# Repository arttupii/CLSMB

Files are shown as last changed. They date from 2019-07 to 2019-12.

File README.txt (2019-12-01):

Closed loop step motor controller

Two modes are supported. Step loss compensation and load position control mode.
You can select mode from config.h file.
     
    Architecture of closed loop step motor controller:

                                             +---------+--------+
                        +---------------+    | Rotary  |  Step  |
                        |               |    | encoder |  Motor |
                        |               |    |         |        |
                        |               |    |         |        |
           stepIn------>|D8             |    |         |        |
                        |   Arduino     |    |         |        |
           dirIn------->|D9 Nano        |    |  A   B  |        |
                        |               |    +---------+--------+
           EnIn-------->|D10            |       |   |     ^^^^
                        |               |IN_A   |   |     ||||
           LED---------<|D13          D2|<------+   |     ||||
                        |               |           |     ||||
        _________       |               |IN_B       |     ||||
        FEED HOLD------<|D7           D3|<----------+     ||||
                        |               |                 ||||
                        |  A2  A1  A0   |                 ||||
                        +---------------+                 ||||
                           |   |   |                      ||||
                           |   |   |                      ||||
                           V   V   V                      ||||
                        +---------------+                 ||||
                        | !EN DIR  STEP |                 ||||
                        |               |                 ||||
                        |  Standard    A|-----red---------+|||
                        |              _|                  ||| 
                        |  Stepmotor   A|-----blue---------+||
                        |               |                   ||  
                        |  controller  B|-----green---------+|
                        |              _|                    |
                        |  e.g. TB6600 B|-----black----------+
                        |               |
                        |               |
                        +---------------+                   

Block diagram (STEP_LOSS_COMPENSATION-mode)
                   +----------------------------------+  
                   |   +----------+                   |  
 Input(Step,En,Dir)|   | Input    |                   |                                             
 ------------------+-->| counter  |                   |                                                  
                       |          |                   |              +--------------+       +--------------+
                   +---|          |                   |              |              |       | Step Motor   |
                   |   +----------+                   V    (Switch)  | Step         |       |              |
                   |                                  +----O         | Motor        |------>|              |
                   |   +----------+   +----------+         ------O-->| Driver       |       |              |
                   +-->|Deviation |   |          |    +----O  ^      | (e.g TB6600) |       |              |
                       |counter   |-->| >n steps |    ^       |      |              |       |              |
                   +-->|          |   |          |    |       |      +--------------+       +--------------+
                   |   +----------+   +---------+     |       |                             | Rotary       |
                   |                        |         |       |                             | encorer      |
                   |                        V         |       |                             |              |
                   |   +----------+      +----------------+   |                             |              |
                   +---|Rotation  |      |                |   |                             +--------------+
                       |position  |      | Fix position   |   |                                    |
                       |counter   |      | (Generate      |---+                                    |     
                   +-->|          |      |step,dir pulses)|                                        |     
                   |   +----------+      +----------------+                                        |     
                   |                                                                               |  
                   +-------------------------------------------------------------------------------+

Block diagram (LOAD_POSITION_CONTROL-mode)
                                                         
                       +----------+                      
 Input(Step,En,Dir)    | Input    |                                                                 
 --------------------->| counter  |                                                                      
                       |          |                                  +--------------+       +--------------+
                   +---|          |                                  |              |       | Step Motor   |
                   |   +----------+                                  | Step         |       |              |
                   |                                                 | Motor        |------>|              |
                   |   +----------+   +----------+    +------------->| Driver       |       |              |
                   +-->|Deviation |   |          |    |              | (e.g TB6600) |       |              |
                       |counter   |-->| >n steps |    |              |              |       |              |
                   +-->|          |   |          |    |              +--------------+       +--------------+
                   |   +----------+   +---------+     |                                     | Rotary       |
                   |                        |         |                                     | encorer      |
                   |                        V         |                                     |              |
                   |   +----------+      +----------------+                                 |              |
                   +---|Rotation  |      |                |                                 +--------------+
                       |position  |      | Fix position   |                                        |
                       |counter   |      | (Generate      |                                        |     
                   +-->|          |      |step,dir pulses)|                                        |     
                   |   +----------+      +----------------+                                        |     
                   |                                                                               |  
                   +-------------------------------------------------------------------------------+

The modes explained: https://www.linearmotiontips.com/how-does-closed-loop-stepper-control-work/
                                    
Hox!
 - Because of speed optimizations you cannot change pinout without code changes. 
 - FEED HOLD is open collector output. With this pin you can ask "feed hold" from CNC machine controller
        steps loss --> FEED HOLD is LOW.
        normally ---> FEED HOLD is open
 - LOAD_POSITION_CONTROL mode needs something. "Direct control" causes too much vibrations. 
 - STEP_LOSS_COMPENSATION mode works
 
List of Known Bugs:
 - You should swap D3 and D8 pins on Arduino nano (this needs also some code changes). StepIn needs RISING interrupt. CHANGE interrupt causes too many interrupts for arduino nano and it cannot handle all of them. This issue has been fixed in ESP2866 branch.

 Compatible with:
     * Arduino nano and Arduino Pro Mini 
     * a standard step motor controller (e.g. a4988 and TB6600)
     * a standard rotary incremental encoder (e.g HN3806-AB-400N, AS5040 or similar)
               +---+   +---+   +---+   +---+
            A -+   +---+   +---+   +---+

              ---+   +---+   +---+   +---+  
            B    +---+   +---+   +---+   +--
     * NEMA xx Stepper motor
 
Demo video: 
https://youtu.be/jLogS5AQ-yQ (AS5040 encoder and A4988 step motor controller)
https://youtu.be/jxansaLNb5I (Serial Plotter view. #define ENABLE_PRINTS 100)

Useful links:
https://www.banggood.com/NANO-IO-Shield-Expansion-Board-Nano-V3-Improved-Version-No-Cable-For-Arduino-p-1010994.html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
https://www.banggood.com/TB6600-Upgraded-Stepper-Motor-Driver-Controller-for-4A-940V-TTL-32-Micro-Step-2-or-4-Phase-of-4257-Stepper-Motor-3D-Printer-CNC-Part-p-14531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
https://www.banggood.com/3D-Printer-42-Stepper-Motor-Drive-Expansion-Board-8825-A4988-p-1028319.html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
https://www.banggood.com/Geeetech-Stepper-Driver-A4988-With-Heatsink-And-Sticker-For-3D-Printer-p-1229214.html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

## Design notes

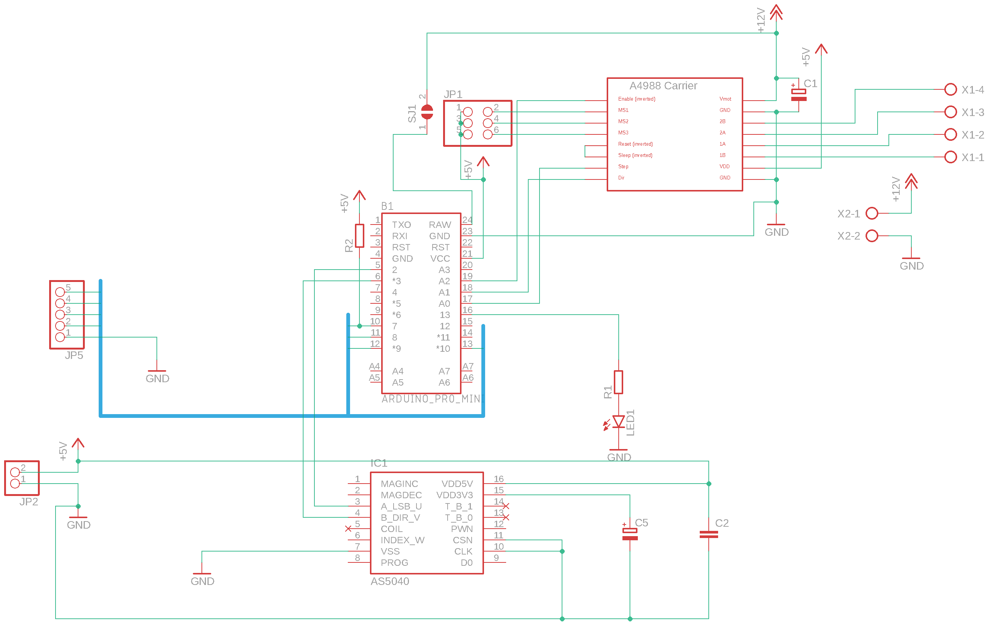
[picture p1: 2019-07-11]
AS5040/schematic.png

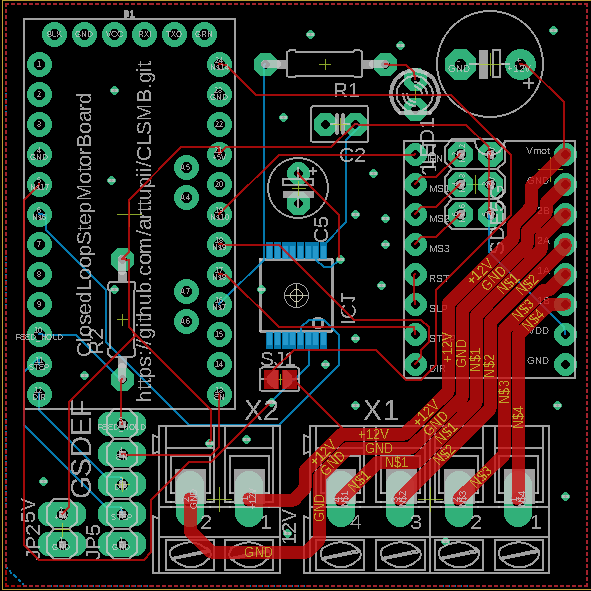
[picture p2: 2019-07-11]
AS5040/board.png

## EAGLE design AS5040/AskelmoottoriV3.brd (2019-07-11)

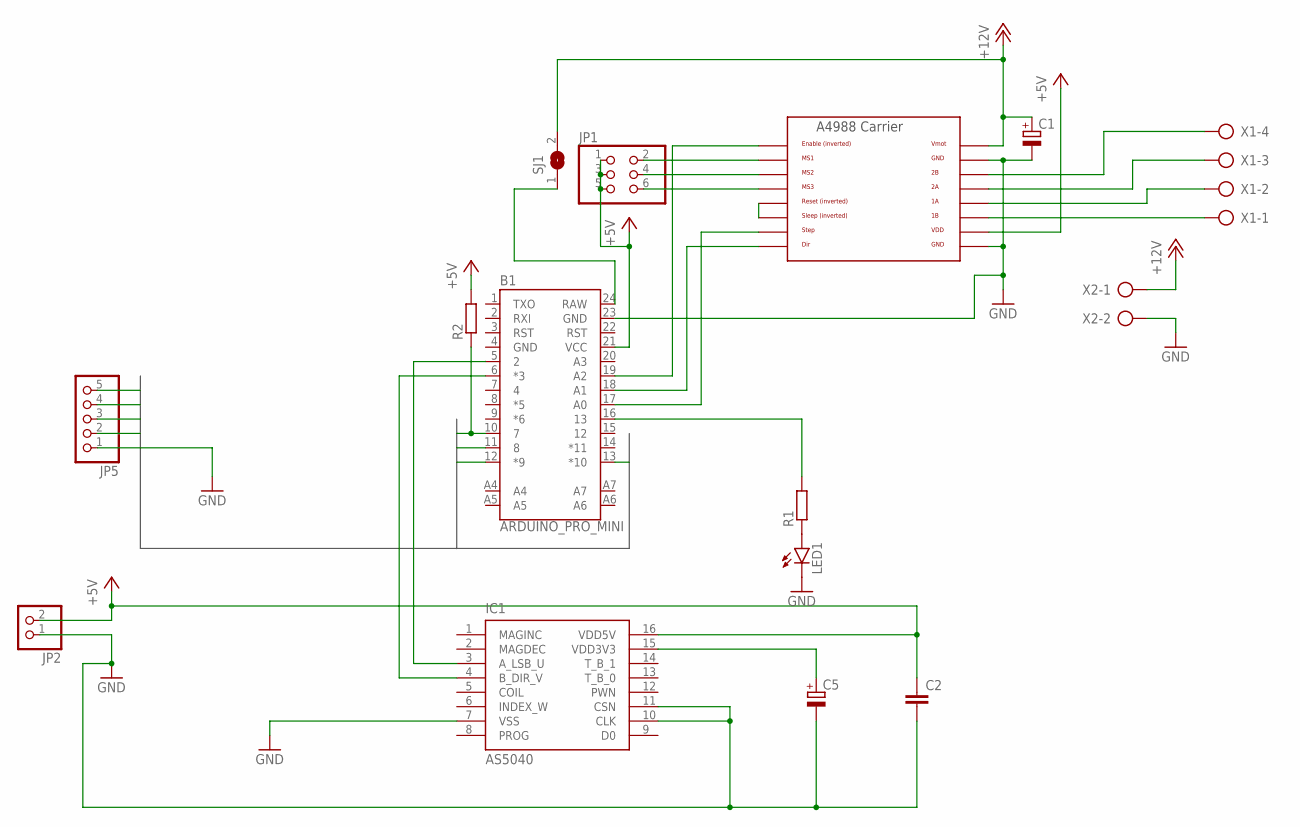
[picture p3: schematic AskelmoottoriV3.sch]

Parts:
B1: ARDUINO_PRO_MINI
C1: CPOL-EUE5-8.5; E5-8,5
C2: C-EU025-030X050; C025-030X050
C5: CPOL-EUE2.5-5; E2,5-5
IC1: AS5040; SSOP16
JP1: PINHD-2X3; 2X03
JP2: PINHD-1X2; 1X02
JP5: PINHD-1X5; 1X05
LED1: LED3MM
R1, R2: R-EU_0207/10; 0207/10
SJ1: SJ
U$1: A4988BREAKOUT
X1: AK300/4
X2: AK300/2

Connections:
+5V: B1.21 (VCC), C2.1, IC1.16 (VDD5V), JP1.1, JP1.3, JP1.5, JP2.2, R2.2, U$1.VDD
+12V: C1.+, SJ1.2, U$1.VMOT, X2.1
DIR: B1.12 (*9), JP5.3
EN: B1.13 (*10), JP5.4
FEED_HOLD: B1.10 (7), JP5.5, R2.1
GND: B1.4 (GND), B1.23 (GND), C1.-, C2.2, C5.-, IC1.7 (VSS), IC1.10 (CLK), IC1.11 (CSN), JP2.1, JP5.1, LED1.K (C), U$1.GND, U$1.GND@0 (GND), X2.2
unnamed: U$1.2B, X1.4
unnamed: U$1.2A, X1.3
unnamed: U$1.1A, X1.2
unnamed: U$1.1B, X1.1
unnamed: B1.6 (*3), IC1.4 (B_DIR_V)
unnamed: B1.16 (13), R1.2
unnamed: B1.17 (A0), U$1.STEP
unnamed: B1.18 (A1), U$1.DIR
unnamed: B1.19 (A2), U$1.EN
unnamed: U$1.RST, U$1.SLP (SLEEP)
unnamed: JP1.2, U$1.MS1
unnamed: JP1.4, U$1.MS2
unnamed: B1.24 (RAW), SJ1.1
unnamed: C5.+, IC1.15 (VDD3V3)
unnamed: JP1.6, U$1.MS3
unnamed: B1.5 (2), IC1.3 (A_LSB_U)
unnamed: LED1.A, R1.1
STEP: B1.11 (8), JP5.2

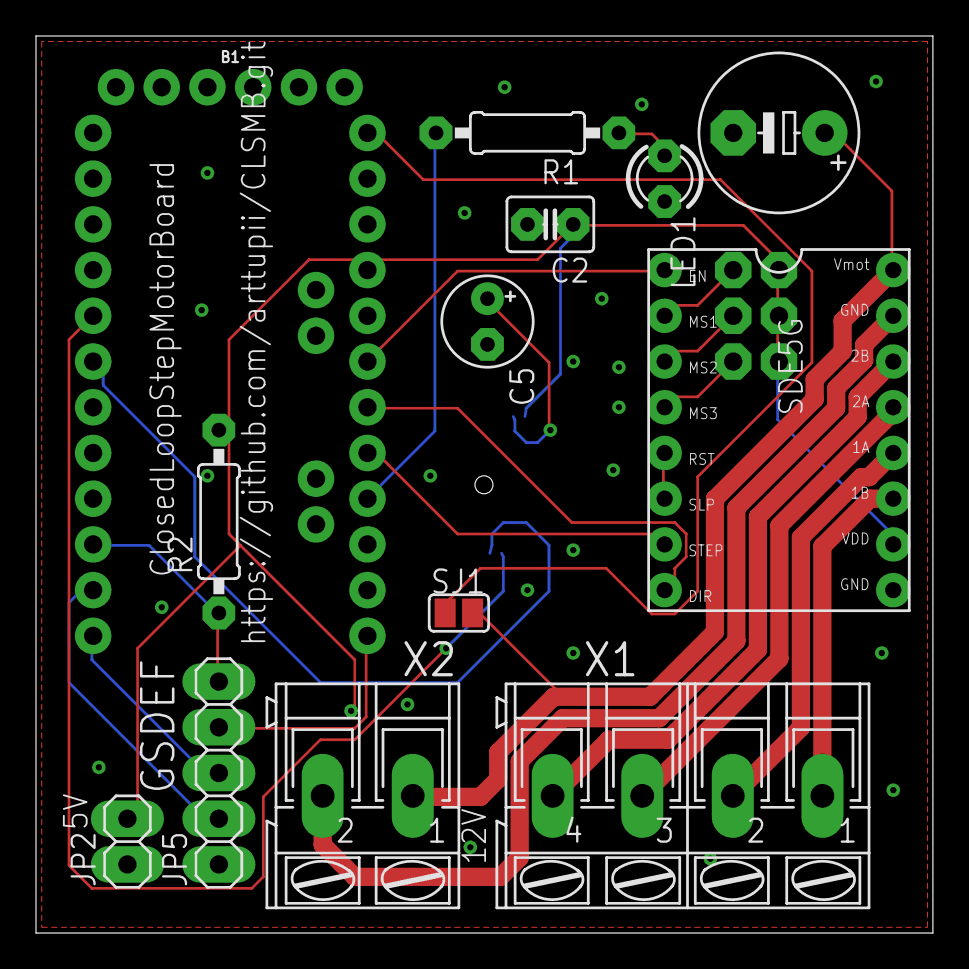
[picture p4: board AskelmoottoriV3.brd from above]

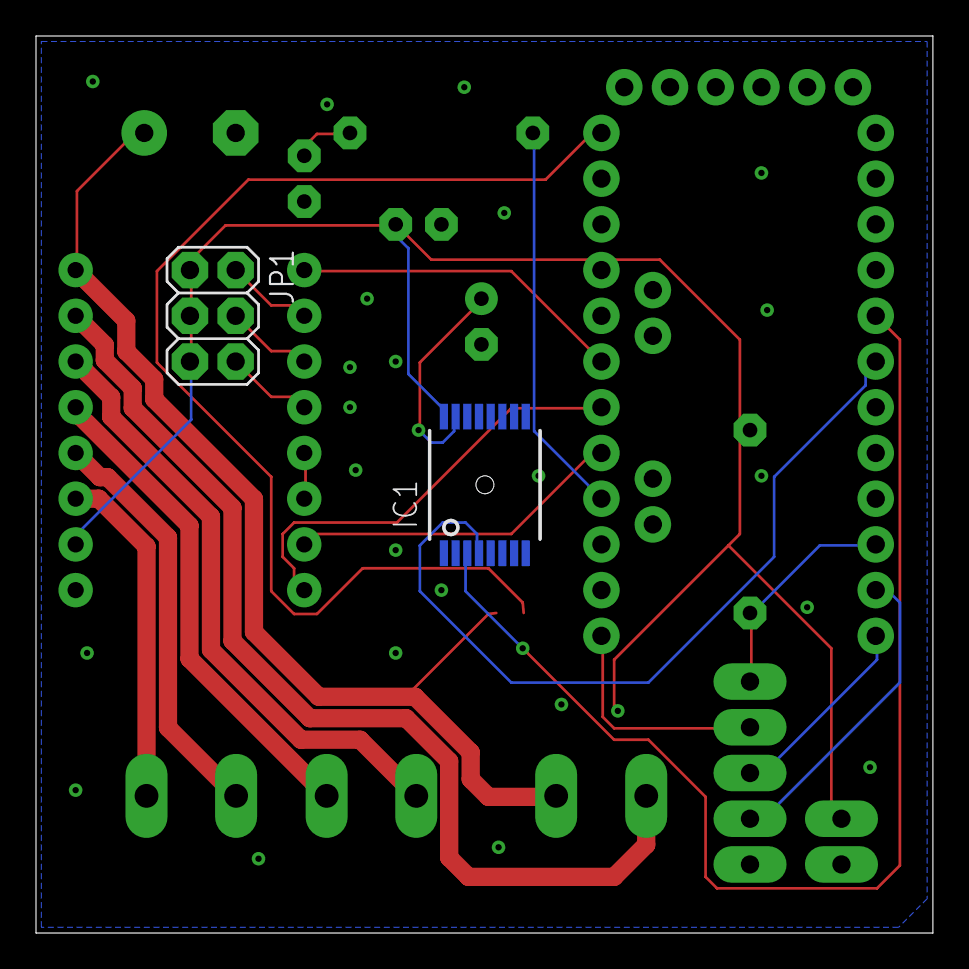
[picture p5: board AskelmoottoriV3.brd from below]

Board: 2 copper layers, 49.8 x 49.8 mm, 15 parts (2 on the bottom side), 24 nets.

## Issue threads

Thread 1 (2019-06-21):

Question about Hardware?

Bastler100, 2019-06-21:
Hello,
are there additional infos about the Hardware/Board, that can be used with this
software?
Thanks
Hans

arttupii, 2019-06-21:
This project has been discontinued (too much other projects)... But I added some files into the repository for you (Readme&schematics).
I have not tested this completely so there might be "some" bugs.

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

Bastler100, 2019-06-22:
Hello Arttupii,
many thanks for your answer. Sorry but I am poor software designer. In the new StepMotorLoop.ino are
new kind of inputs: "IN_STEP0 and IN_STEP1"? Do you think its possible to change the software for universal controller. A standartstepper with a encoder heds or similar( inkremental output a + b ), a standart motor driver and a Arduino nano with build in usb-connector. So it will be able to use the controller with all kind of stepper with related driver?
Thanks
Hans

Bastler100, 2019-06-22:
Hallo Arttuppi,many thanks for your answer. I send a additional question in git. May be there other user interstet.
Thanks Hans

-----Ursprüngliche Mitteilung-----
Von: arttupii <notifications@github.com>
An: arttupii/CLSMB <CLSMB@noreply.github.com>
Cc: Bastler100 <HaHoLang@aol.com>; Author <author@noreply.github.com>
Verschickt: Sa, 22. Jun. 2019 0:54
Betreff: Re: [arttupii/CLSMB] Question about Hardware? (#1)

This project has been discontinued (too much other projects)... But I added some files into the repository for you (Readme&schematics).
I have not tested this completely so there might be "some" bugs.—
You are receiving this because you authored the thread.
Reply to this email directly, view it on GitHub, or mute the thread.

Bastler100, 2019-06-22:
Hallo Arttuppi,many thanks for your answer. I send a additional question in git. May be there are other users interestet.
Thanks Hans

-----Ursprüngliche Mitteilung-----
Von: arttupii <notifications@github.com>
An: arttupii/CLSMB <CLSMB@noreply.github.com>
Cc: Bastler100 <HaHoLang@aol.com>; Author <author@noreply.github.com>
Verschickt: Sa, 22. Jun. 2019 0:54
Betreff: Re: [arttupii/CLSMB] Question about Hardware? (#1)

This project has been discontinued (too much other projects)... But I added some files into the repository for you (Readme&schematics).
I have not tested this completely so there might be "some" bugs.—
You are receiving this because you authored the thread.
Reply to this email directly, view it on GitHub, or mute the thread.

arttupii, 2019-06-22:
Hi,
> In the new StepMotorLoop.ino are new kind of inputs: "IN_STEP0 and IN_STEP1"?

IN_STEP1 define can be removed. It is not used.

>  Do you think its possible to change the software for universal controller. A standartstepper with a encoder heds or similar( inkremental output a + b ), a standart motor driver and a Arduino nano with build in usb-connector. So it will be able to use the controller with all kind of stepper with related driver?

You can use any Arduino board that has at least two external interrupt pins (nano is ok).
A rotatery encoder could be a problem if your rotatery encoder uses quadrature signal.
The current code doesn't support quadrature signals without modifications (you must rewrite interrupt functions). Only step/direction incremental signal is supported.

Bastler100, 2019-06-23:
Hello Arttuppi,
I will attempt to build your controller with a taller pcb and a stronger stepper driver like a TB6600
to mount it on a NEMA34-Stepper. When I was successful I send here e message.

Thanks
Hans

arttupii, 2019-06-24:
Check this commit. I added the support of quadrature incremental encoder.
https://github.com/arttupii/CLSMB/commit/8436964e7d9ab23bf52f8aa9e3ca032da2d34b26

Bastler100, 2019-06-24:
Hello Arttuppi,
many thanks for your answer. My idea for incremental input was to use a standart incremental encoder
without the AS5040. I will now attempt to create a PCB  for the first code and will order some from a china pcb manufactorer. In dimensions for mounting on a NEMA34 stepper.
Thanks
Hans

Bastler100, 2019-06-24:
Hello Arttuppi,
I want to use an encoder, because it is very difficult to solder the small ssop16 package, the Arduino
had only to read the A + B signal and need no power for controlling the AS5040, and I have some open frame encoders in my stock.
Thanks
Hans

arttupii, 2019-06-24:
> My idea for incremental input was to use a standart incremental encoder
without the AS5040.

That's what I thought. Now you can use standard encoder without coding changes (just enable QUADRATURE_MODE flag).
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

Bastler100, 2019-06-26:
Hello Arttuppi,
in the code are librarys used. Can you tell me where I can find the micros.h and the millis.h library.
Its possible to use the last code with a standart encoder or with the AS5040 in incremental mode?
In this case it will be required to set the AS5040 in incremental mode about OTP-Mode-Register.

Thanks
Hans

Bastler100, 2019-06-26:
Hello Arttuppi,
I see you create a new code for the mode with standart encoder. I think there is now a code for the encoder and an other code for the AS5040. Do you think its possible to show both codes in the Git?
Is the serial operation for a dro? Can I deactivate the serial operation?
Thanks
Hans

arttupii, 2019-06-26:
Hi,

>  Can you tell me where I can find the micros.h and the millis.h library.

Millis.h is in here: https://github.com/arttupii/ArduinoHelperLibrary

> Its possible to use the last code with a standart encoder or with the AS5040 in incremental mode? In this case it will be required to set the AS5040 in incremental mode about OTP-Mode-Register.

I removed "Step / Dir-Mode" support. You can now only use quad A/B-Mode. Luckily it is a default mode for AS5040, so you don't need to modify OPT-Mode-Registers anymore.  Just connect AS5040 and arduino nano  to each other.  Also standard encoders are using Quad A/B-Mode as default (e.g. HN3806-AB-400N).
So, the same code supports now AS5040 and standard encoders...  But the circuit board must be redesigned because of latest code changes (and quad A/B-mode). :(

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

> Do you think its possible to show both codes in the Git?

The same code supports now AS5040 and a standard encoder. We just now use quad A/B-Mode instead of Step / Dir-Mode in AS5040.

> Is the serial operation for a dro? Can I deactivate the serial operation.

Yes it is... You can deactivate it.

Bastler100, 2019-06-26:
Hello,many thanks for your answer. I will try to build a working axis.
Hans

-----Ursprüngliche Mitteilung-----
Von: arttupii <notifications@github.com>
An: arttupii/CLSMB <CLSMB@noreply.github.com>
Cc: Bastler100 <HaHoLang@aol.com>; Author <author@noreply.github.com>
Verschickt: Mi, 26. Jun. 2019 21:21
Betreff: Re: [arttupii/CLSMB] Question about Hardware? (#1)

Hi,
Can you tell me where I can find the micros.h and the millis.h library.
Millis.h is in here: https://github.com/arttupii/ArduinoHelperLibrary
Its possible to use the last code with a standart encoder or with the AS5040 in incremental mode? In this case it will be required to set the AS5040 in incremental mode about OTP-Mode-Register.
I removed "Step / Dir-Mode" support. You can now only use quad A/B-Mode. Luckily it is a default mode for AS5040, so you don't need to modify OPT-Mode-Registers anymore. Just connect AS5040 and arduino nano to each other. Also standard encoders are using Quad A/B-Mode as default (e.g. HN3806-AB-400N).
So, the same code supports now AS5040 and standard encoders... But the circuit board must be redesigned because of latest code changes (and quad A/B-mode). :(

Do you think its possible to show both codes in the Git?
The same code supports now AS5040 and a standard encoder. We just now use quad A/B-Mode instead of Step / Dir-Mode in AS5040.
Is the serial operation for a dro? Can I deactivate the serial operation.
Yes it is... You can deactivate it.—
You are receiving this because you authored the thread.
Reply to this email directly, view it on GitHub, or mute the thread.
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
arttupii, 2019-07-11:
Hi, Looks like stm32 is very cheap chip, so it would be ok (perfect) for this use. But I think Arduino Nano is enough.
At least when we reduce the number of pulses. In the latest code, you can now select resolution of the encoder. You can double or quadruples the resolution of the encoder. Or just use 1x resolution.

arttupii, 2019-07-11:
Hi, I also changed pin map. A/B signals are connected now D2&D3 pins on Arduino Nano. Thanks for the comments.

Bastler100, 2019-07-16:
Hello Arttuppi,in the Git is a shematic with a ProMini. I make a picture with connections for the stepper.Will you be so kindly check the connections?
Many thanks for your support
 Hans

-----Ursprüngliche Mitteilung-----
Von: arttupii <notifications@github.com>
An: arttupii/CLSMB <CLSMB@noreply.github.com>
Cc: Bastler100 <HaHoLang@aol.com>; Author <author@noreply.github.com>
Verschickt: Do, 11. Jul. 2019 19:32
Betreff: Re: [arttupii/CLSMB] Question about Hardware? (#1)

Hi, I also changed pin map. A/B signals are connected now D2&D3 pins on Arduino Nano. Thanks for the comments.—
You are receiving this because you authored the thread.
Reply to this email directly, view it on GitHub, or mute the thread.

arttupii, 2019-07-16:
Hi, No problemo. I can check the connections.

Bastler100, 2019-07-25:
Hello Arttupii,I draw a pcb 50x50mm with a pro mini, a as5601 and a drv8825. I want
to mill it,but the footprint from the as5601 was to small, so i orderd
some pcbs in China. Have you an idea for driver with more current fora nema 34 or 42?Thanks
 Hans

-----Ursprüngliche Mitteilung-----
Von: arttupii <notifications@github.com>
An: arttupii/CLSMB <CLSMB@noreply.github.com>
Cc: Bastler100 <HaHoLang@aol.com>; Author <author@noreply.github.com>
Verschickt: Di, 16. Jul. 2019 20:14
Betreff: Re: [arttupii/CLSMB] Question about Hardware? (#1)

Hi, No problemo. I can check the connections.—
You are receiving this because you authored the thread.
Reply to this email directly, view it on GitHub, or mute the thread.

arttupii, 2019-07-29:
Hi,

My plan is use nema23, TB6600, HN3806-AB-400N rotation encoder and arduino nano (+ extension board https://tinyurl.com/y2pt8n8q) in my cnc router. TB6600 gives max 5A. TB6600 and nema23 because my cnc router uses them currently and I don't see any reason replace them. AS5040&A4988 solution is for my delta 3D printer.
I have no other ideas or plans.

Bastler100, 2019-07-29:
Hello Arttupii,many thanks for your answer. I have also some stepper driver with the TB6600. I will use theAS5601 because its not so difficult to solder. Hans

-----Ursprüngliche Mitteilung-----
Von: arttupii <notifications@github.com>
An: arttupii/CLSMB <CLSMB@noreply.github.com>
Cc: Bastler100 <HaHoLang@aol.com>; Author <author@noreply.github.com>
Verschickt: Mo, 29. Jul. 2019 22:40
Betreff: Re: [arttupii/CLSMB] Question about Hardware? (#1)

Hi,My plan is use nema23, TB6600, HN3806-AB-400N rotation encoder and arduino nano (+ extension board https://tinyurl.com/y2pt8n8q) in my cnc router. TB6600 gives max 5A. TB6600 and nema23 because my cnc router uses them currently and I don't see any reason replace them. AS5040&A4988 solution is for my delta 3D printer.
I have no other ideas or plans.—
You are receiving this because you authored the thread.
Reply to this email directly, view it on GitHub, or mute the thread.

Bastler100, 2019-09-11:
Hello Arttupii,I get now the PCBs from China to control these steppers. I use the ProMini and the AS5601.Hans

-----Ursprüngliche Mitteilung-----
Von: arttupii <notifications@github.com>
An: arttupii/CLSMB <CLSMB@noreply.github.com>
Cc: Bastler100 <HaHoLang@aol.com>; Author <author@noreply.github.com>
Verschickt: Do, 11. Jul. 2019 19:32
Betreff: Re: [arttupii/CLSMB] Question about Hardware? (#1)

Hi, I also changed pin map. A/B signals are connected now D2&D3 pins on Arduino Nano. Thanks for the comments.—
You are receiving this because you authored the thread.
Reply to this email directly, view it on GitHub, or mute the thread.

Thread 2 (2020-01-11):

did not work with pro mini

rizpardazan, 2020-01-11:
hello dear
with wireing like in readme file , with arduino pro mini , did not work
it seems can not count quadruples encoder.

arttupii, 2020-01-11:
Hi,
Could you test your quadrature encoder with this simple test code?

1. Flash Pro mini with test code
2. Open  tools->Serial Plotter
3. Set baud rate to 115200
4. Try to rotate quadrature encoder. You should now see A and B signals on plotter.

```c++
#define PIN_IN_A     5
#define PIN_IN_B     4

void setup() {
  Serial.begin(115200);
  pinMode(PIN_IN_A, INPUT_PULLUP);
  pinMode(PIN_IN_B, INPUT_PULLUP);
}

void loop() {
  Serial.print(digitalRead(PIN_IN_A)*3+5);
  Serial.print(" ");
  Serial.println(digitalRead(PIN_IN_B)*3);
}
```

rizpardazan, 2020-01-12:
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

yes , this code work,
in main code , encoder A and B will be connected to pin 4 and 5 or 2 and 3 in pro mini ?

arttupii, 2020-01-12:
Sorry, I thought (read) you are using esp2866 chip and ESP2866 branch (I know you wrote arduino pro mini, but but I read it somehow wrongly).

You can try to remove line #define FLIP_ENCODER from config.h file. If it doesn't work you can try to enable debug prints. Set ENABLE_PRINTS to 60 from config.h (it prints values of internal_encoder_position and motor_position). If everything works ok, internal_encoder_position value should increase when motor_position value increases and  internal_encoder_position value should decrease  when motor_position decreases.

Please be aware about that there are known bug in master branch and you should swap D3 and D8 pins on 8-bit Arduino (this needs also some code changes. I have no time do this :(). StepIn needs RISING interrupt. CHANGE interrupt causes too many interrupts for 8-bit arduino and it starts losing pulses at high speed. This issue has been fixed in ESP2866 branch.

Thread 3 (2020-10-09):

Works the closed loop with a Arduino ProMicro?

Bastler100, 2020-10-09:
Hello Arttupii,
do you know if the closed loop software works with a Arduino ProMicro? The Arduino-Software
has compiled the code without mistake. The board is smaller than a Nano or Mini and has a build
in USB-Port.
Thank
Hans

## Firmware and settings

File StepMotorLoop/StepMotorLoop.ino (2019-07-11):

#include <avr/interrupt.h>
#include "config.h"

volatile long internal_in_stepCounter = 0;
volatile long internal_encoder_position = 0;
volatile bool motorJamming = false;

unsigned short calculateOCR1A(unsigned short preScaler, float us) {
  const float u = 1.0 / (16000000.0 / preScaler);
  float ret = (float(us) / (u * 1000000));
  return ret;
}

void setup() {
#if ENABLE_PRINTS>0
  Serial.begin(230400);
  Serial.println("Starting...");
#endif

  cli();

  //Step Motor controller pins to output
  DDRC = 0b00000111;

  //Set input pins (step_in, dir_in and en_in) and output pin (LED)
  DDRB =  0b00100000;
  PORTB = 0b00000111;

  //Set input pins (A, B) and HOLD_ON (as open state).
  DDRD =  0b00000000;
  PORTD = 0b00110000;

  cli();//Disable interrupts
  //See https://sites.google.com/site/qeewiki/books/avr-guide/external-interrupts-on-the-atmega328


  //enable interupts for EN&STEP
  PCICR = 0b00000001; //Enable PCIE0 

  PCMSK0 = 0b00000101; //Pin Change Mask Register. Enable Pin change interrupt for PCINT02 (EN pin) & PCINT00 (STEP_IN)
 
  // initialize Timer1
  TCCR1A = 0;    // set entire TCCR1A register to 0
  TCCR1B = 0;    // set entire TCCR1A register to 0

  #ifdef X1_ENCODING
  EIMSK = 0b01;//External Interrupt Flag Register. Enable Interrupt for A/B signals
  EICRA = 0b0011;//External Interrupt Control Register A
  #endif
  #ifdef X2_ENCODING
  EIMSK = 0b01;//External Interrupt Flag Register. Enable Interrupt for A/B signals
  EICRA = 0b0001;//External Interrupt Control Register A
  #endif
  #ifdef X4_ENCODING
  EIMSK = 0b11;//External Interrupt Flag Register. Enable Interrupt for A/B signals
  EICRA = 0b0101;//External Interrupt Control Register A
  #endif 
  //Enable Compare A Interrupt
  bitSet(TIMSK1, OCIE1A);

  long step_pulse_width_us = (1000000.0 / (NEMA_MOTOR_PPR * STEP_MOTOR_REV_PER_SEC)) / 2;
  if (step_pulse_width_us >= 1048560L) { //1048560L = (1/(16MHz/256))*0xffff    (256=prescaler)
    OCR1A = calculateOCR1A(1024, step_pulse_width_us);
    TCCR1B = 0b101; //prescaler 1024
  } else if (step_pulse_width_us >= 262140L) {
    OCR1A = calculateOCR1A(256, step_pulse_width_us);
    TCCR1B = 0b100; //prescaler 256
  } else if (step_pulse_width_us >= 32767) {
    OCR1A = calculateOCR1A(64, step_pulse_width_us);
    TCCR1B = 0b011; //prescaler 64
  } else if (step_pulse_width_us >= 4095) {
    OCR1A = calculateOCR1A(8, step_pulse_width_us);
    TCCR1B = 0b010; //prescaler 8
  } else {
    OCR1A = calculateOCR1A(1, step_pulse_width_us);
    TCCR1B = 0b001; //prescaler 1
  }

  sei();//Enable interrupts
}

inline void printDebugInfoToSerialPlotter() {
  static unsigned long t = millis();
  if ((millis() - t) > 100) {
    t = millis();
#ifdef STEP_LOSS_COMPENSATION_MODE
    Serial.println(calculateErrorStepLossCompensationMode());
#endif
  }
}

void loop() {
  runMotor();
#if ENABLE_PRINTS>99
  printDebugInfoToSerialPlotter();
#endif
}

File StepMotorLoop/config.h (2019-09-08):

#ifndef __CONFIG__H_
#define __CONFIG__H_

#define ENCODER_PULSES_PER_REV 256.0 //State change per Revolution (A+B) (AS5040)
//#define ENCODER_PULSES_PER_REV 400.0 //State change per Revolution (A+B) (HN3806-AB-400N)


#define NEMA_MOTOR_FULL_STEPS 200.0
#define NEMA_MOTOR_MICROSTEPS 16
#define NEMA_MOTOR_PPR (NEMA_MOTOR_FULL_STEPS * NEMA_MOTOR_MICROSTEPS)


#define FLIP_ENCODER //enable if rotor position repairing is done wrong direction

//Select loop back mode
//https://www.linearmotiontips.com/how-does-closed-loop-stepper-control-work/
#define STEP_LOSS_COMPENSATION_MODE
//#define LOAD_POSITION_CONTROL_MODE


#define ENABLE_PRINTS 1

#define STEP_1_PULSE_US 1 //pulse wide


#ifdef STEP_LOSS_COMPENSATION_MODE
  #define STEP_ERROR_MAX 200 //Start position repairing if position deviation is more than this
  #define STEP_ERROR_MIN 10 //Stop position repairing if position deviation is less than this
  #define STEP_MOTOR_REV_PER_SEC 2.0 //revolutions/second. Fixing speed
#endif

#ifdef LOAD_POSITION_CONTROL_MODE
  #define STEP_MOTOR_REV_PER_SEC 4.0 //revolutions/second. Fixing speed
  #define STEP_ERROR_MAX 2 //Start position repairing if position deviation is more than this
  #define STEP_ERROR_MIN 1 //Stop position repairing if position deviation is less than this
#endif

//Modes explained https://www.linearmotiontips.com/what-is-quadrature-encoding/
//#define X1_ENCODING   // 1x the resolution of the encoder
//#define X2_ENCODING //doubles the resolution of the encoder
#define X4_ENCODING //quadruples the resolution of the encoder

#ifdef X1_ENCODING
 #define ENCODER_RESOLUTION (ENCODER_PULSES_PER_REV)
#endif
#ifdef X2_ENCODING
 #define ENCODER_RESOLUTION (2*ENCODER_PULSES_PER_REV)
#endif
#ifdef X4_ENCODING
 #define ENCODER_RESOLUTION (4*ENCODER_PULSES_PER_REV)
#endif


#ifdef STEP_LOSS_COMPENSATION
  #ifdef LOAD_POSITION_CONTROL
    #error "Selected STEP_LOSS_COMPENSATION & LOAD_POSITION_CONTROL!!"
  #endif
#endif
#endif

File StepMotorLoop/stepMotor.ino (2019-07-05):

#define SET_MOTOR_STEP_LOW  PORTC&=0b11111110
#define SET_MOTOR_STEP_HIGH PORTC|=0b00000001

#define SET_MOTOR_DIR_LOW  PORTC&=0b11111101
#define SET_MOTOR_DIR_HIGH PORTC|=0b00000010

#define READ_EN_PIN (PINB & 0b00000100)

#define HOLD_ON_REQ DDRD|=0b10000000 //HOLD_ON is LOW. Use D7 pin like open collector output
#define CANCEL_HOLD_ON_REQ DDRD&=0b01111111 //HOLD_ON is OPEN

#define SET_LED_HIGH PORTB|=0b00100000
#define SET_LED_LOW PORTB&=0b11011111

const u8 defaultDivider = (1000000.0 / (NEMA_MOTOR_PPR*STEP_MOTOR_REV_PER_SEC))/(2*20);

volatile u8 dir;
volatile u8 nextStep = 0;
volatile u8 divider = defaultDivider;

ISR(TIMER2_OVF_vect) {       // timer compare interrupt service routine
  TCNT2 = 245;  //-->20us
  if (divider <= 0) {
    if (dir) {
      if(nextStep) {
        if (dir == 1) {
          SET_MOTOR_DIR_HIGH;
        } else {
          SET_MOTOR_DIR_LOW;
        }
        SET_MOTOR_STEP_HIGH;
        nextStep = 0;
      } else {
        SET_MOTOR_STEP_LOW;
        nextStep = 1;
      }
    }
    divider = defaultDivider;
  }
  divider--;
}

static Millis ledOnTimer = Millis(200);
Micros u;

inline void runMotor() {
  if (READ_EN_PIN) {
    motorJamming=false;
    return;
  }
  dir = checkErrorDirection();
  
  if (dir) {
    motorJamming = true;
    HOLD_ON_REQ;
    SET_LED_HIGH;
    ledOnTimer.reset();
  } else {
    nextStep = 0;
    motorJamming = false;
    divider = defaultDivider;
    CANCEL_HOLD_ON_REQ;
    if (ledOnTimer.check()) {
      SET_LED_LOW;
    }
  }
}

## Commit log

2019-06-21 Add schematic&gerber files + README
    [AskelmoottoriV3.brd, AskelmoottoriV3.sch]
2019-06-26 Removed eagle&photo files
    [AskelmoottoriV3.brd, AskelmoottoriV3.sch]
2019-06-26 FEED HOLD pin
2019-06-27 AS5040 board&Schematic files
    [AskelmoottoriV3.brd, AskelmoottoriV3.sch]
2019-06-27 Demo code
    [AskelmoottoriV3.brd, AskelmoottoriV3.sch]
2019-06-27 Add debug prints
2019-06-27 Improve debug prints
2019-07-01 Update eagle files
    [AskelmoottoriV3.brd, AskelmoottoriV3.sch]
2019-07-02 Add crosshair
    [AskelmoottoriV3.brd, AskelmoottoriV3.sch]
2019-07-03 Gerber files
2019-07-05 Run step motor in ISR(TIMER2_OVF_vect)
2019-07-05 Remove dependency to Millis()
2019-07-11 Add quadrature encoding X1, X2 and X3 modes
    [AskelmoottoriV3.brd, AskelmoottoriV3.sch]

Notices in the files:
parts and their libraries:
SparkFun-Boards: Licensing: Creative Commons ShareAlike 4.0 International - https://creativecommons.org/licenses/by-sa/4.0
